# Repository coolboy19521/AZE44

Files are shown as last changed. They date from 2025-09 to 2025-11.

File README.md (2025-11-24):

<h1>AZE - 44 Team Report</h1>



<table align="center" cellspacing="0" cellpadding="0" style="margin:0; padding:0; border-collapse:collapse;">
  <tr>
    <th colspan="2">Team Photos</th>
  </tr>
  <tr>
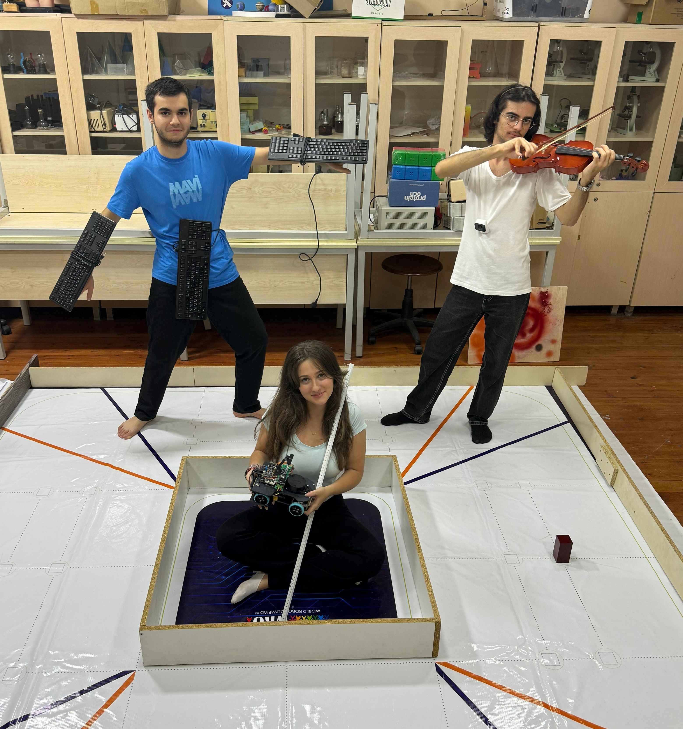
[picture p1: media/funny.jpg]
    <td align="center" style="margin:0; padding:0;"><br><b>Funny Photo</b></td>
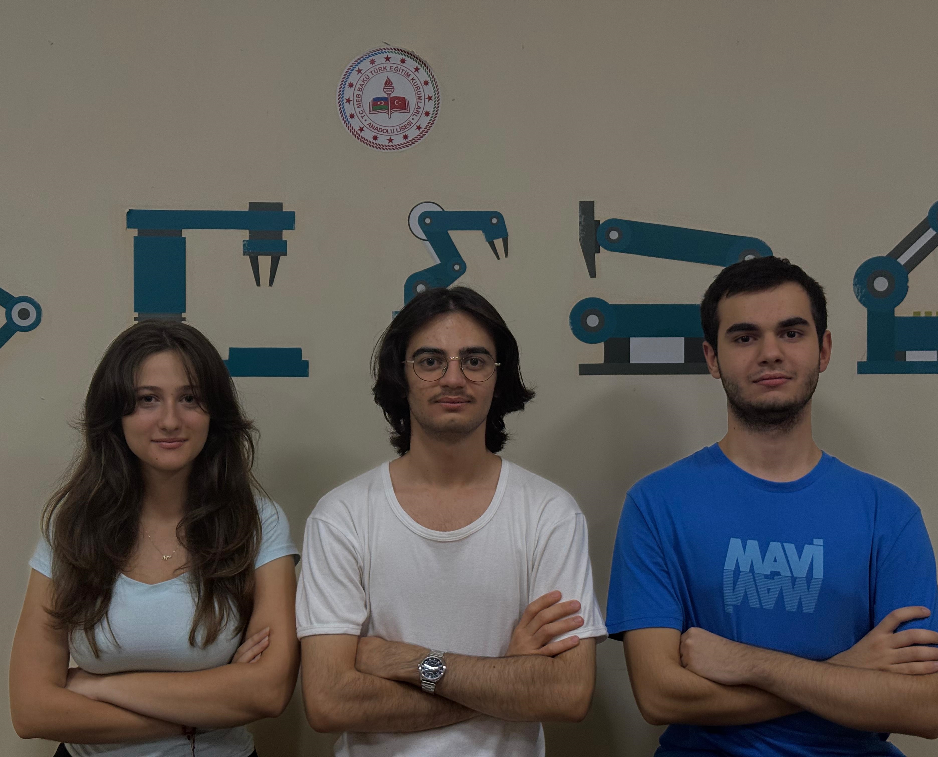
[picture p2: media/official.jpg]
    <td align="center"><br><b>Official Photo</b></td>
  </tr>
</table>

Our team consists of 3 members: Eyyub Şenal (center in the official photo), Əhməd Qəmbərli (rightmost in the official photo), and Melisa Yıldız (leftmost in the official photo). Everyone in this team has an experience of WRO at least at national level. Eyyub and Melisa have even participated at international stages. Eyyub received a silver medal in WRO 2023 Panama and Melisa received a gold medal in WRO 2024 İzmir. Here are communication informations for our team:

- Eyyub Şenal from [Bakı Türk Anadolu Liseyi](https://btal.meb.k12.tr/):
  - <a href="mailto:arduinoaz2022@gmail.com" style="text-decoration:none;">
      
      arduinoaz2022@gmail.com
    </a>
  - <a href="https://www.instagram.com/shenaleyup?igsh=MWpqMHJieTc5MXM1Ng==">
      
      shenaleyup
    </a>

- Əhməd Qəmbərli from [Bakı Türk Anadolu Liseyi](https://btal.meb.k12.tr/):
  - <a href="mailto:ehmedqemberli09@gmail.com">
      
      ehmedqemberli09@gmail.com
    </a>
  - <a href="https://discord.gg/your_discord_invite">
      
      coolboy19521
    </a>

- Melisa Yıldız from [Bakı Türk Anadolu Liseyi](https://btal.meb.k12.tr/):
  - <a href="mailto:melisa.17.yildiz@gmail.com">
      
      melisa.17.yildiz
    </a>
  - <a href="https://www.instagram.com/melisa_yildiz_17?igsh=MWN1cGxsMXF5YndtOQ==">
      
      melisa_yildiz_17
    </a>

> [!NOTE]
> Fun fact: Every pair of our team members' have worked as a team before. It is first time that we are working as a trio.

Before the national qualification our work schedule was very full, we were working every day before the competition. We started in summer so we had plenty of time during the holiday. After qualifying to the international finals we had to limit how much we work every week, because we had school, exams and a **personal life**. We worked every Monday, Wednesday, Thursday and Saturday. On Sundays we had a meeting about the improvements over the week and what we are planning to do next week.

<h1>Our Robot</h1>

<table cellspacing="0" cellpadding="0" style="margin:0; padding:0; border-collapse:collapse;">
  <tr>
    <th colspan="4">Robot Photos</th>
  </tr>
  <tr>
    <td align="center" colspan="2">
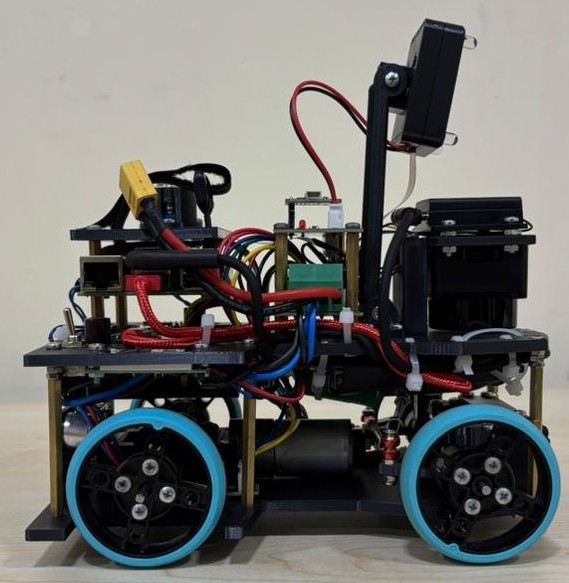
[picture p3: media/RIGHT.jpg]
      <br>
      <b>Right</b>
    </td>
    <td align="center" colspan="2">
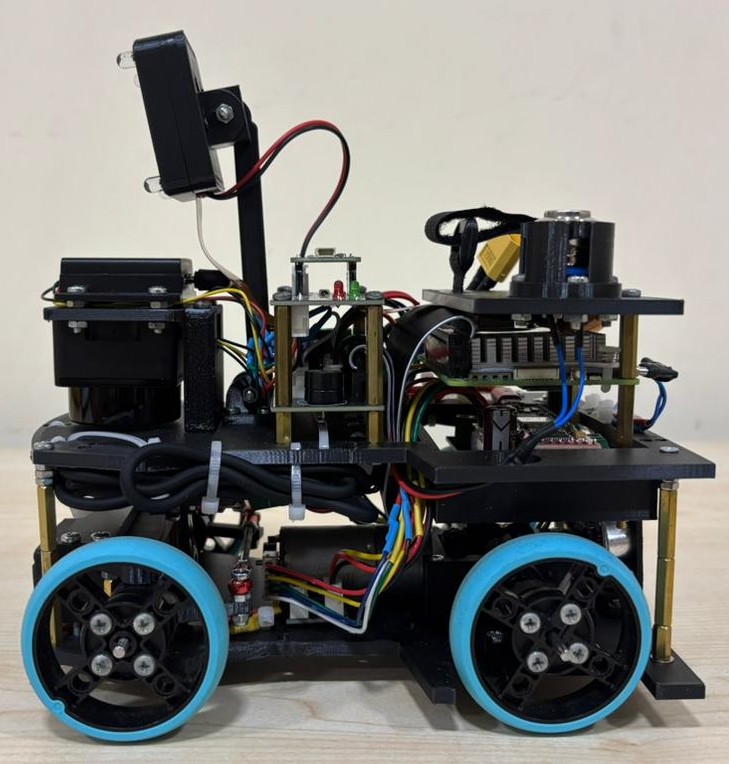
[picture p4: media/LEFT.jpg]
      <br>
      <b>Left</b>
    </td>
  </tr>
  <tr>
    <td align="center">
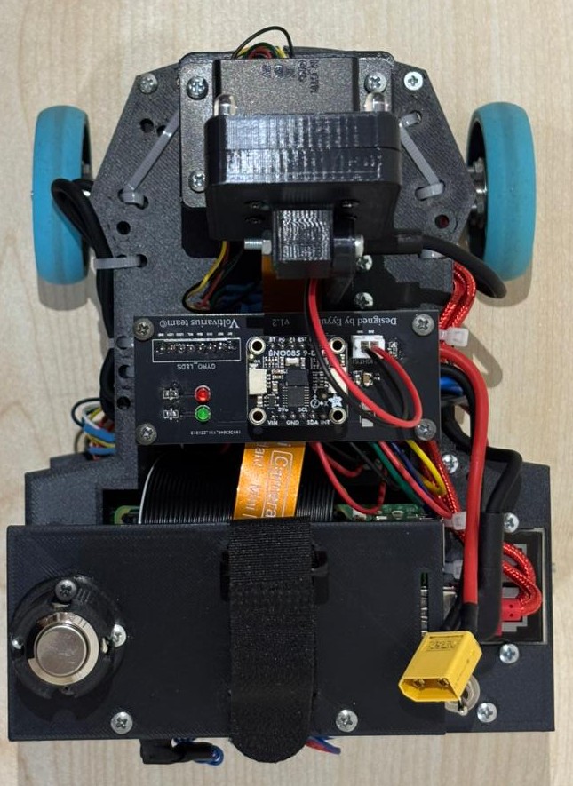
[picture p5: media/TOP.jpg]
      <br>
      <b>Top</b>
    </td>
    <td align="center">
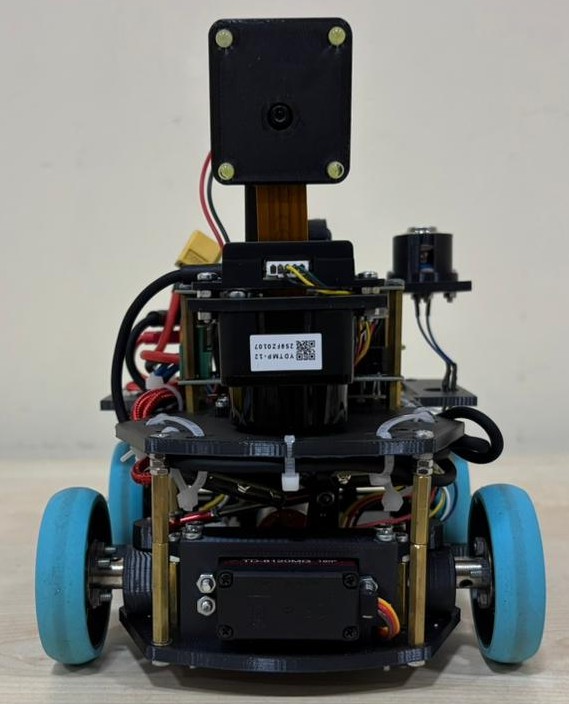
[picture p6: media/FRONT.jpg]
      <br>
      <b>Front</b>
    </td>
    <td align="center">
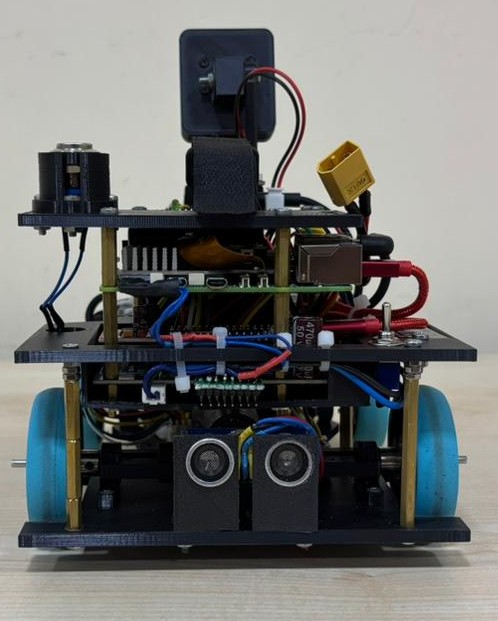
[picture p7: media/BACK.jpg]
      <br>
      <b>Back</b>
    </td>
    <td align="center">
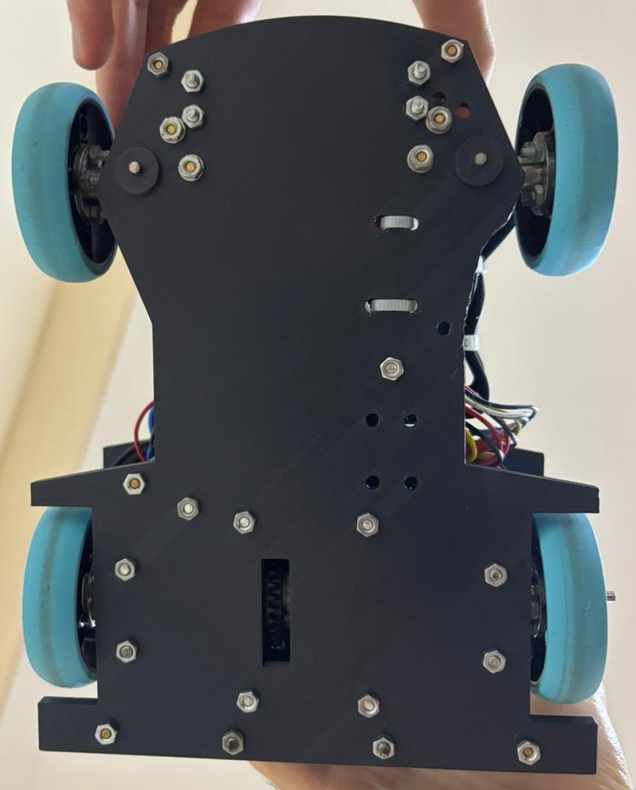
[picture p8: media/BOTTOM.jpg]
      <br>
      <b>Bottom</b>
    </td>
  </tr>
</table>

Our robot is called “miav”. Miav is a ROS2-based four-wheeled mobile robot developed on the Raspberry Pi 5 platform. It integrates advanced hardware including a T-MINI-Plus Lidar TOF, a BNO085 IMU, and a Raspberry Pi Camera for color detection.

<h1>Table of Contents</h1>

### [Evolution of our robot](/EVOL.md)
### [Philosophy and habits](/PHIL.md)
### [Electronics documentation](/schemes/README.md)
### [Mechanics documentation](/models/README.md)
### [Software documentation](/src/README.md)
### [Videos](/videos/README.md)
### [Team photos](/t-photos/README.MD)
### [Robot photos](/v-photos/README.md)
<hr>

<p align="center">
  <picture>
  <source media="(prefers-color-scheme: dark)" srcset="media/my_image.png">
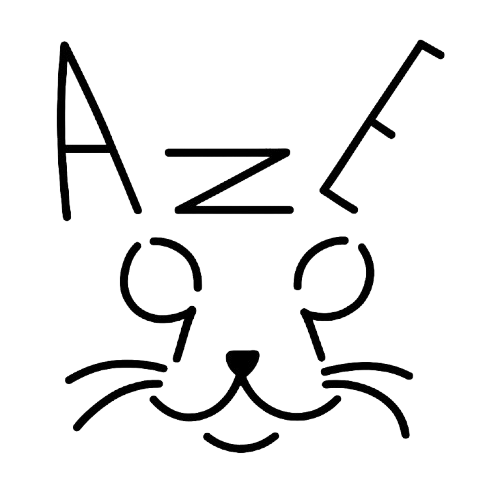
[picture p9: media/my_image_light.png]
  
  </picture>
</p>

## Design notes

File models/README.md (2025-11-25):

>[!IMPORTANT]
>This README file includes some gifs, which could be best viewed through the GitHub itself. You might need to wait for some GIFs to load as well.

>[!IMPORTANT]
>There are some heavy videos inside this README file. Please wait until the page is fully loaded before proceeding.

# 1. Bill of Materials (BOM)

<table align="center">
  <tr>
    <th colspan="4">Mechanics</th>
  </tr>

  <tr>
    <th>Component</th><th>Picture</th>
    <th>Component</th><th>Picture</th>
  </tr>

  <tr>
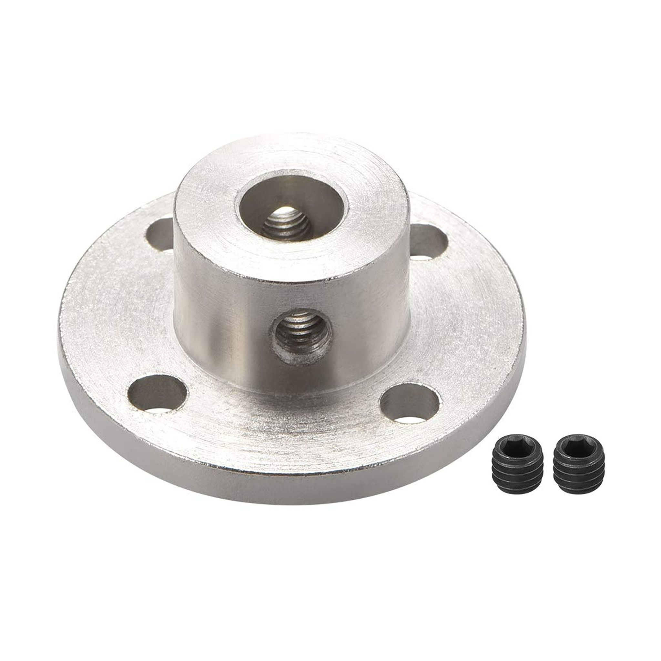
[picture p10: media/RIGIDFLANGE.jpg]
    <td>3mm Rigid Flange Coupling x 4</td><td></td>
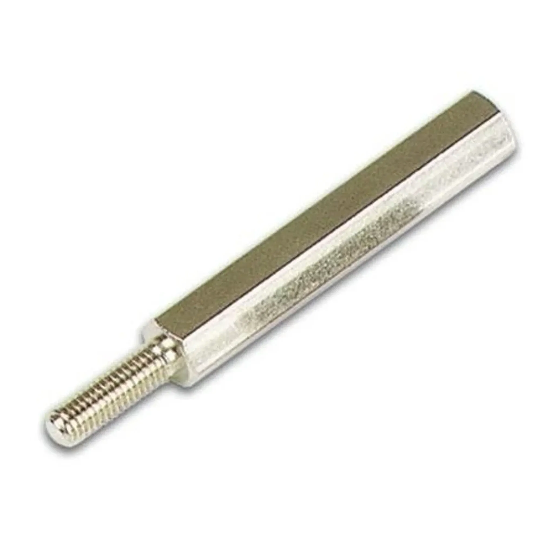
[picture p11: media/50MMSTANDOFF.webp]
    <td>50mm Standoff Female-Male x 6</td><td></td>
  </tr>

  <tr>
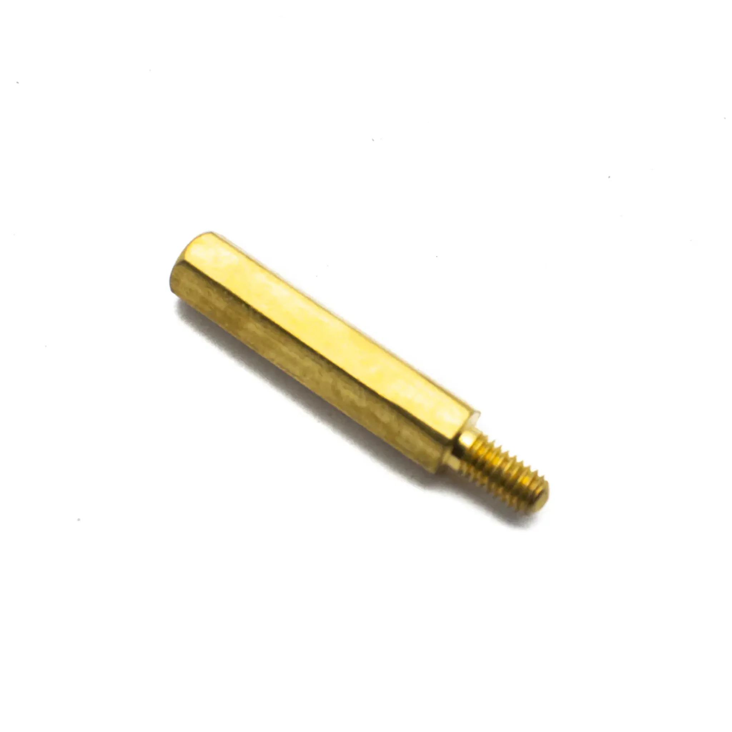
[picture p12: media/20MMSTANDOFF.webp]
    <td>20mm Standoff Female-Male x 4</td><td></td>
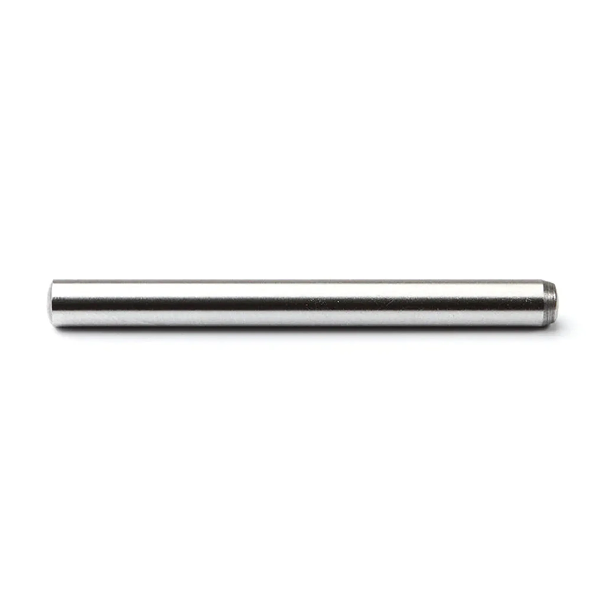
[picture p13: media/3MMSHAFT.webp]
    <td>3mm Shaft 7cm x 2</td><td></td>
  </tr>

  <tr>
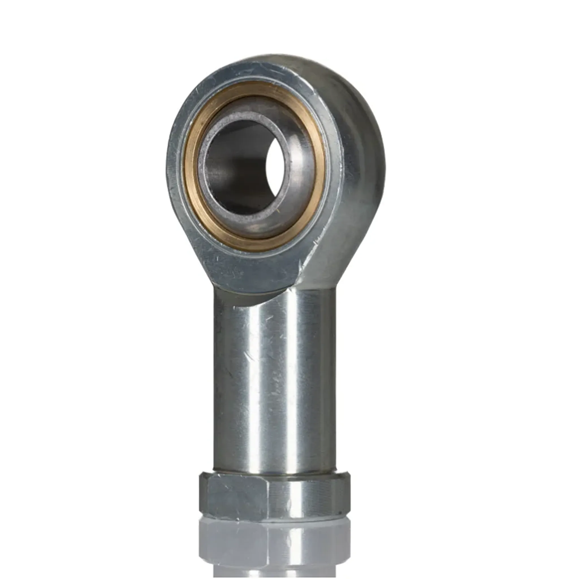
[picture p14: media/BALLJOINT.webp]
    <td>Ball Joint x 4</td><td></td>
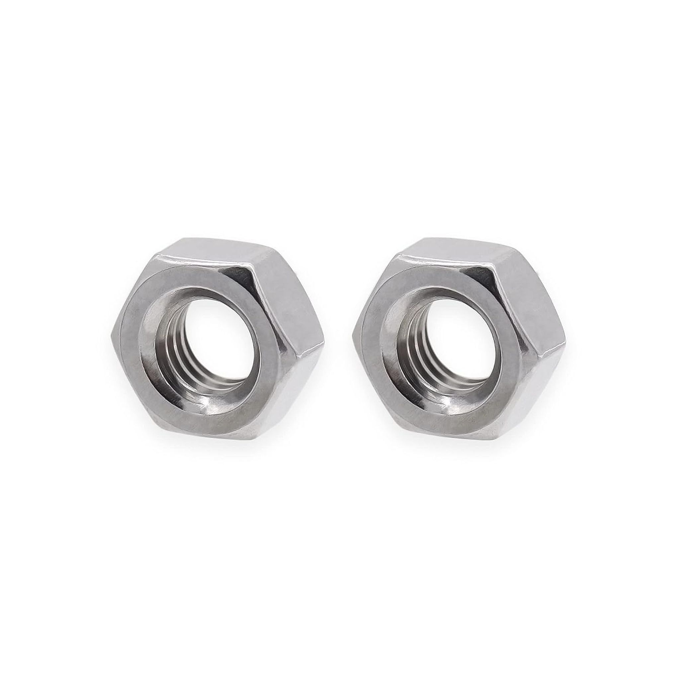
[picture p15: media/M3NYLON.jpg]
    <td>M3 Nylon Insert Lock Nut x 2</td><td></td>
  </tr>

  <tr>
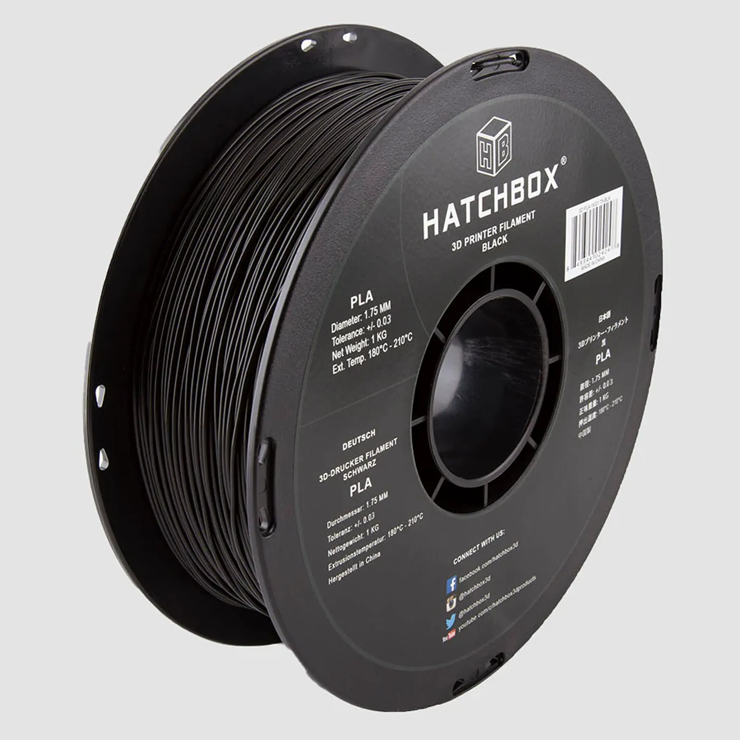
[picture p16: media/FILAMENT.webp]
    <td>Filament 1Kg x 1</td><td></td>
  </tr>
</table>

# 2. The  Chassis and General Design

We have a 2-platform design in our robot, which we preferred to be able to modify or repair the robot easily during our test and potentially the competition.

- It only takes our robot a few seconds to remove its top platform,
- We can access the circuitry, sensors, and other internal mechanics so that we can work on them immediately. This saved us so much time when we working on our robot.

The initial design for our chassis was very narrow with angled corners. Although it was sufficient enough for our initial testing, it was very unstable at higher speeds and tended to tip over easily when we added more parts to it. We first analyzed how our mass is distributed and where our center of gravity is, then we decided to completely revamp our design and resize our chassis to `15cm` in width and `28cm` in length. After the modifications, we were able to increase the stability of our robot so that our sensors, which include the camera and LIDAR, are protected from damage caused by vibrations.

-	We printed the 3D parts with PLA and the Sidewinder X2, 
-	along with a nozzle temperature of `210°C` and a heated bed temperature of `60°C`. Where we felt we needed additional strength, for example, in our shafts and our link rods, we chose to work with aluminum. Additionally, the robot weighs `1400g`.

The earlier versions of robots did not support complex steering or mounting points for sensors and other factors, but with the new design, it has become more modular, and ready for the Ackermann steering mechanism.

<table align="center">
  <tr>
    <th colspan="2">Top Chassis Mechanical Drawings</th>
  </tr>
  <tr>
    <td align="center">
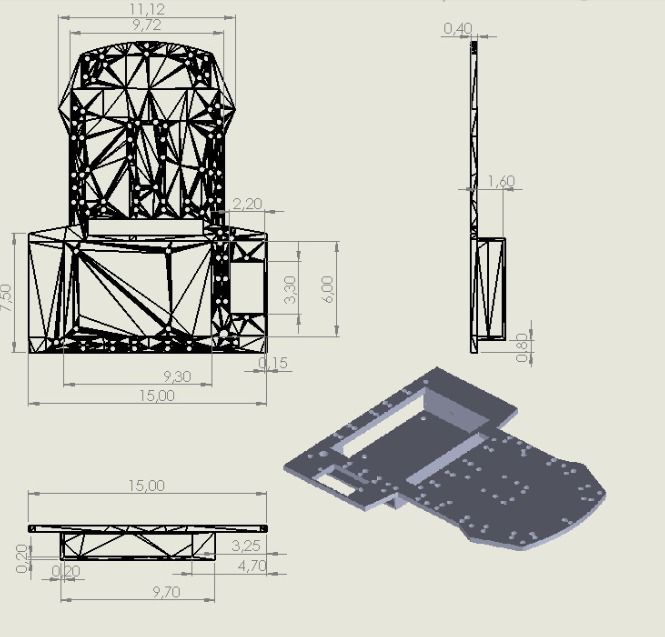
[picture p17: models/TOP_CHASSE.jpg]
      <br>
      <b>Top Chassis</b>
    </td>
    <td align="center">
      <br>
      <b>Printing Proccess</b>
    </td>
  </tr>
</table>
<br>
<table align="center" cellspacing="0" cellpadding="0" style="margin:0; padding:0; border-collapse:collapse;">
  <tr>
    <th colspan="4">Bottom Chassis Mechanical Drawings</th>
  </tr>
  <tr>
    <td align="center" colspan="2">
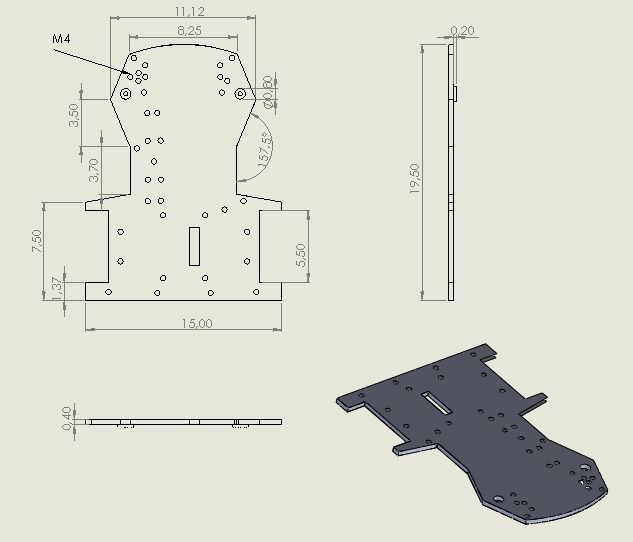
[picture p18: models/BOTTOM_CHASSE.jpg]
      <br>
      <b>Bottom Chassis</b>
    </td>
    <td align="center" colspan="2">
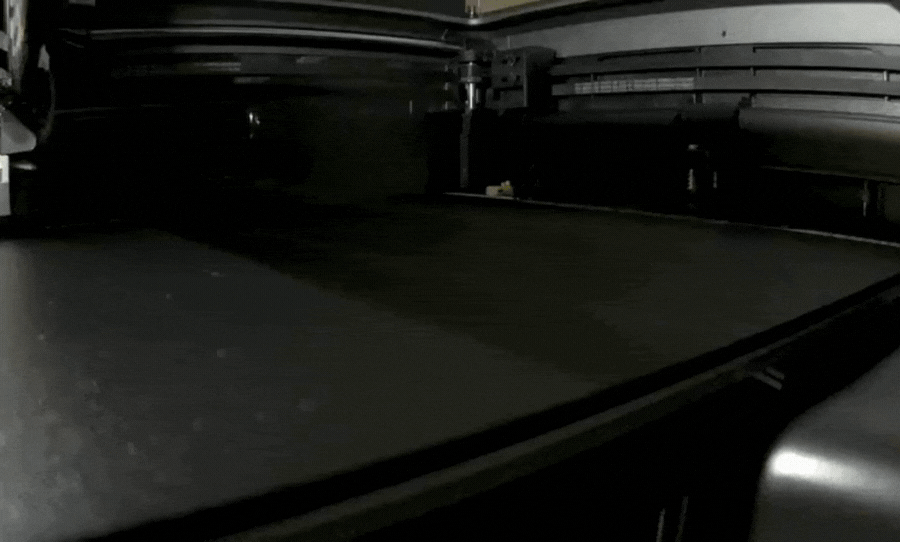
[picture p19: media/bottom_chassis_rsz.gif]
      <br>
      <b>Bottom Chassis Printing Proccess</b>
    </td>
  </tr>
</table>

# 3. Drive System and Gearbox

We use a `12V` DC motor as our drive motor for our robot.

-	It draws about `320mA` on average with no load and revolves at a speed of up to `450RPM`.
-	Although our robot weighs `1400g`, if we rely on this motor directly, it may result in insufficient torque for our robot to glide smoothly, especially when our robot accelerates. Because of this, we decided to create a gearbox to possess a ratio of `2:3` using our 3D printer.

Below is the formula for the torque gained from this ratio:

$$\large T_{\text{output}} = T_{\text{motor}} \times \frac{3}{2}$$

How it works:
- The power generated from the motor is transmitted to the central gear and
- then it is transmitted to the other two wheels in the rear part of the vehicle. 

We also modeled the gearbox to work similarly to how a differential works. This means that when one wheel stops revolving, for example, when it hits something or meets more friction, the other can continue revolving. This way we make sure that it does not get stuck or lose its pace.

We printed the gears themselves and the gearbox with the PLA material, with aluminum shafts on which the gears are mounted. We also placed metal ball bearings on every rotating shaft, including rear wheels and gearbox connections, for our robot to work smoothly, instead of causing excessive wear to our gears to decrease friction. The metal ball bearings are 693ZZ.

<table align="center" cellspacing="0" cellpadding="0" style="margin:0; padding:0; border-collapse:collapse;">
  <tr>
    <th colspan="4">Gearbox Mechanical Drawings</th>
  </tr>
  <tr>
    <td align="center" colspan="2">
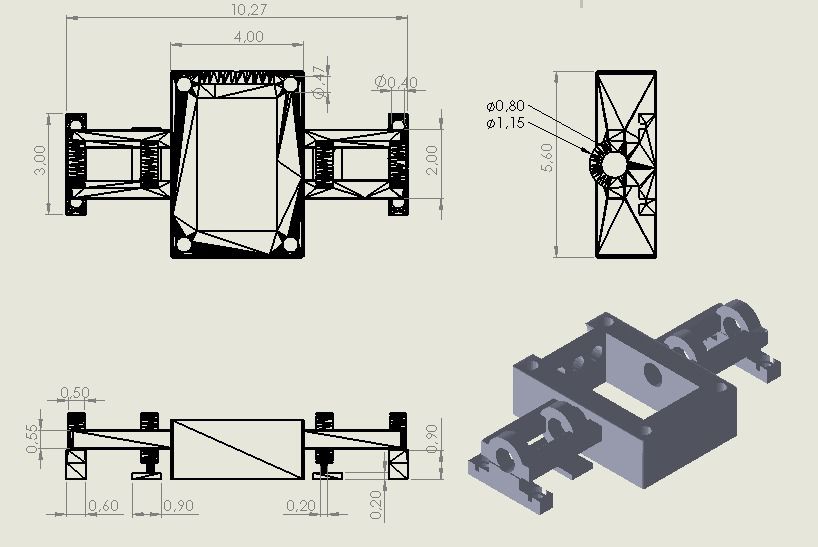
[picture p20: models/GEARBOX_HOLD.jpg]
      <br>
      <b>Gearbox</b>
    </td>
    <td align="center" colspan="2">
      <br>
      <b>Printing Proccess</b>
    </td>
  </tr>
</table>

<br>

<div>
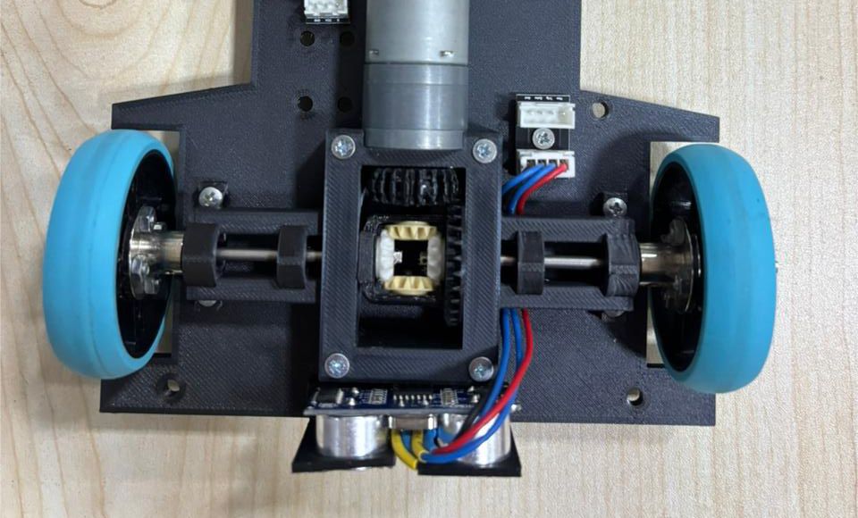
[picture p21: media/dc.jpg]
DC System
  
  <p style="margin-top:0;"><i>Figure 1.1: DC System</i></p>
</div>

# 4. Ackermann Steering System

One of the most important changes that we integrated into our design is the Ackermann steering system. We didn’t use this mechanism in our previous versions of the robots, where we could only manage to implement either turning mechanisms with semi-fixed angles and less accurate steering mechanisms. After we saw the difficulties that the previous systems were causing, wedecided to design the entire steering mechanism from scratch.
The principle behind Ackermann steering is that for a turn, the inner wheel has to turn at a sharper angle than the outer wheel. This corresponds to the geometric shape described by circular motion, where each wheel essentially has to turn at a slightly different radius than the other. After we applied the Ackermann principle, we were finally able to ensure that no wheels start to slide and that the robot moves in predictable arcs.

The formula for the relationship between steering angle is:

$$\large \frac{\tan(\theta_\text{inner})}{\tan(\theta_\text{outer})} = \frac{L}{L + T}$$

L is wheelbase and T is track width. The correct formula using turning radius is:

$$\large \frac{1}{\tan(\theta_\text{inner})} = \frac{1}{R} - \frac{D}{2H} \quad \large ; \quad \large \frac{1}{\tan(\theta_\text{outer})} = \frac{1}{R} + \frac{D}{2H}$$

Our front wheel distance is 13 cm, and our wheelbase (distance between our front and rear axle) is 11 cm. As I’ve already mentioned, the measurements were all established according to the Ackermann mechanism, which ensure that both wheels turn at angles and are still in sync.

In our steering system we used:
-	Aluminum link arms that are mounted to 3D-printed steering knuckles and a PLA servo mount. 
-	We coupled the link arms with 3-mm aluminum rods, and all pivot points are equipped with 693ZZ bearings to ensure uniform movement. 
-	The steering power comes from a TD8120MG metal-gear servo. The servo acts on one link arm, and its action is transmitted through the Ackermann design to turn the wheels by the right amount. This way we make sure that our robot has a smooth turning action.

It is also important to notice and emphazie that the Ackermann steering is implemented in actual vehicles as well,
-	To reduce wear on tires, 
-	Enhance turning precision, and 
-	Provide better control at both high and low velocities. For us, its implementation in our robot allowed our vehicle to act similarly to actual vehicles and enhance the turning precision in our navigation significantly.

<table align="center">
  <tr>
    <th colspan="2">Ackermann Wheel Holder Mechanical Design</th>
  </tr>
  <tr>
    <td align="center">
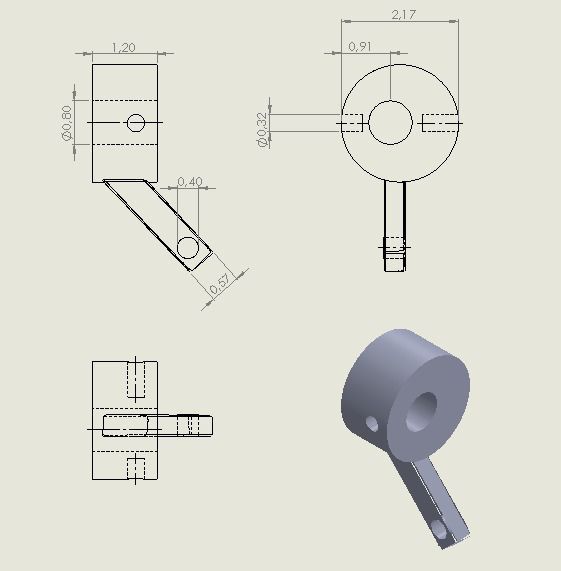
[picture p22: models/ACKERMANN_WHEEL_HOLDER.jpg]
      <br>
      <b>Ackermann Wheel Holder</b>
    </td>
    <td align="center">
      <br>
      <b>Printing Proccess</b>
    </td>
  </tr>
</table>

<br>

<div>
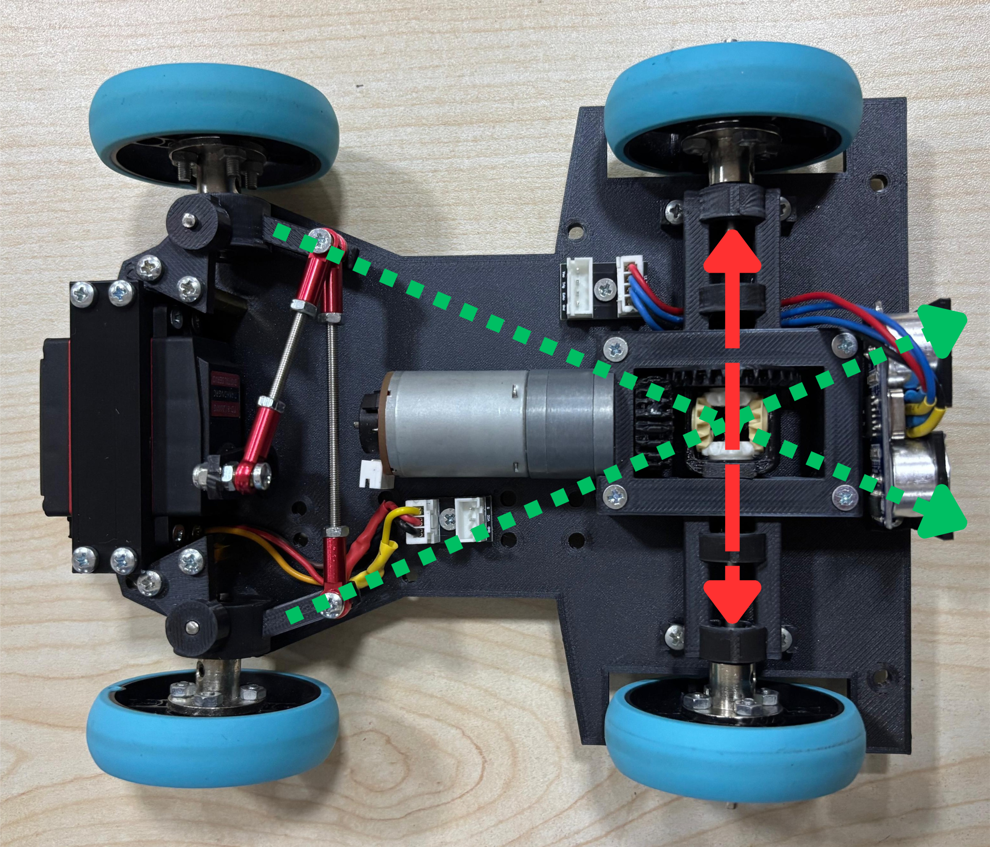
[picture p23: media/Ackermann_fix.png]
Ackermann System
  
  <p style="margin-top:0;"><i>Figure 2.1: Ackermann System</i></p>
</div>

>[!NOTE]
>The dotted lines here represent the imaginary projection of a straight line aligned perfectly with the tire holders. The intersection point of these lines should align to the center of the track perfectly for a functional ackermann system. In our previous robot we had miscalculated it a little bit, and the intersection point was a little bit away from the track. That's why this time we focused on fixing the problem. An accurate ackermann system provides us better steering possibilities.

# 5. Servo System

The servo that controls the steering mechanism is the TD8120MG metal gear servo. It has a torque of around 18 kg-cm at 4.8 volts and about 20 kg-cm at 6 volts, which is ideal for the rotation of the wheels. The servo also requires about 1.1 seconds to rotate 360 degrees, so it enables fast steering.

We placed the servo on top of a bracket created using PLA, and we specifically designed this bracket to make sure that it aligns well with the Ackermann linkage mechanism. As the servo rotates, it acts on the main steering arm, which in turn acts on both front wheels using the Ackermann rods.

<table align="center" cellspacing="0" cellpadding="0" style="margin:0; padding:0; border-collapse:collapse;">
  <tr>
    <th colspan="4">Servo Holder Mechanical Design</th>
  </tr>
  <tr>
    <td align="center" colspan="2">
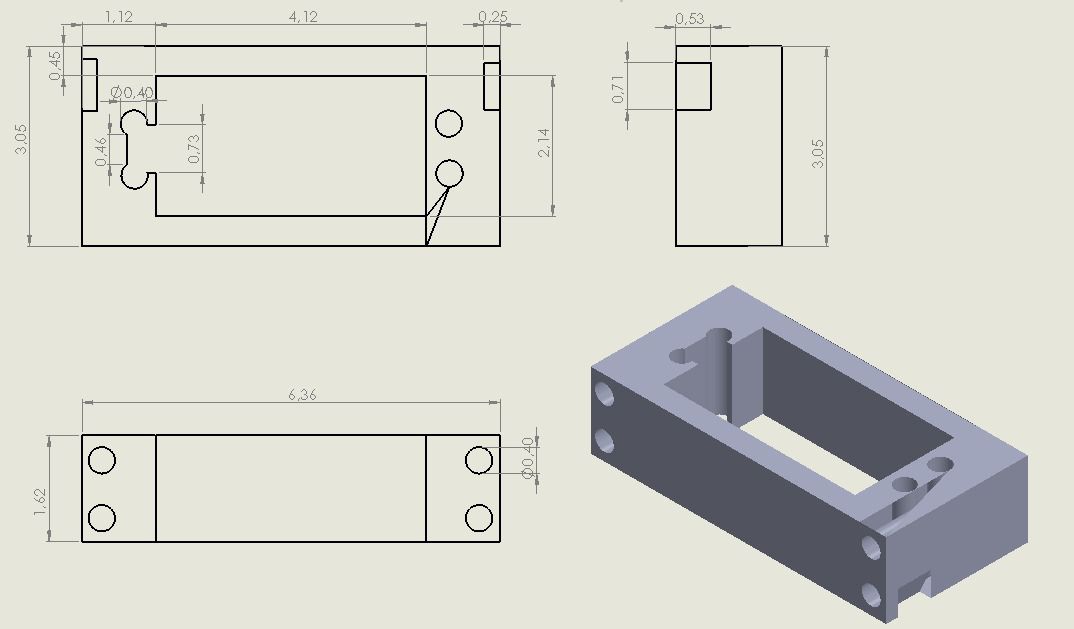
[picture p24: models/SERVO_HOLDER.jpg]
      <br>
      <b>Servo Holder</b>
    </td>
    <td align="center" colspan="2">
      <br>
      <b>Printing Proccess</b>
    </td>
  </tr>
</table>

# 6. Wheel Movement
-	We control the movement of the wheels on our robot with the rear DC motor. As the rear wheels rotate clockwise, they propel the robot forward.
-	The the rotation of the motor in an anticlockwise direction makes the robot go backward. 
-	With the gearbox on the robot we are able to ensure that if one wheel faces a rotation problem or a mechanical barrier in general, the other wheel continues to rotate.

# 7. Center of Gravity and Weight Distribution
We also positioned every element on our robot to ensure its center of mass remains near the center. Liked this, we increase the robot’s balance and make sure it doesn't develop nose or tail lift during acceleration or braking.

-	We placed The LIDAR near to the front but slightly above the center because we wanted to provide our robot with a full scan range. 
-	The camera sensor is placed on its 75-degree width-wise PLA bracket to allow it to scan most of its environment and identify objects-the colors-effectively. 
-	Lastly, at the back, we mounted the ultrasonic sensor to assist our robot in detecting objects while reversing or turning through its track on the map.
-	In the middle of the bottom platform, we put the battery that helps balance out the heavier parts on top, such as the Raspberry Pi and motor driver. We placed the components in this particular way because we wanted our vehicle to have very stable movement when driving, especially during higher speeds while turning.

The formula of the center of mass is:

$$\large X_\text{cm} = \frac{\sum_{i=1}^{n} x_i \times m_i}{\sum_{i=1}^{n} m_i} \quad \large ; \quad Y_\text{cm} = \frac{\sum_{i=1}^{n} y_i \times m_i}{\sum_{i=1}^{n} m_i} \quad \large ; \quad Z_\text{cm} = \frac{\sum_{i=1}^{n} z_i \times m_i}{\sum_{i=1}^{n} m_i}$$

So applying this formula to our robot:

- Total mass $$\large \text{M}$$ = 1400 g.
- Coordinate system: (0,0) = front-left corner. 𝑥to the right (0–15 cm), 𝑦to the rear (0–19 cm).
- Component positions $$\text{(x, y)}$$ in cm and masses 𝑚in g:
1.	Battery: $$\large \text{m}$$ = 300, $$\text{(x, y)}$$ = (4,1)
2.	Raspberry Pi: $$\large \text{m}$$ = 45, $$\text{(x, y)}$$ = (4,1)
3.	Lidar: $$\large \text{m}$$ = 18, $$\text{(x, y)}$$ = (7.5,2)
4.	Servo: $$\large \text{m}$$ = 55, $$\text{(x, y)}$$ = (7.5,6)
5.	Encoder motor: $$\large \text{m}$$ = 120,	$$\text{(x, y)}$$ = (2,16)
6.	Motor driver: $$\large \text{m}$$ = 40, $$\text{(x, y)}$$ = (7.5,9)
7.	Camera: $$\large \text{m}$$ = 10,	$$\text{(x, y)}$$ = (7.5,0.5)
8.	BNO085: $$\large \text{m}$$ = 8,	$$\text{(x, y)}$$ = (6,10)
9.	Ultrasonic : $$\large \text{m}$$ = 15,	$$\text{(x, y)}$$ = (7.5,19)
10.	Amper monitor: $$\large \text{m}$$ = 30,	$$\text{(x, y)}$$ = (10,12)
11.	Misc (connectors, resistors, fuse, SD, etc.): $$\large \text{m}$$ = 20, $$\text{(x, y)}$$ = (7.5,9)
12. Chassis + mechanical + wheels: $$\large \text{m}$$ = 739, $$\text{(x, y)}$$ = (7.5,9.5)

$$\large \sum_{i=1}m_i$$ = 300 + 45 + 18 + 55 + 120 + 40 + 10 + 8 + 15 + 30 + 20 + 739 = 1400 g

$$\large \sum_{i=1}m_i \times x_i$$ = 1200 + 180 + 135 + 412.5 + 240 + 300 + 75 + 48 + 112.5 + 300 + 150 + 5542.5 = 8695.5

$$\large X_\text{cm} = \frac{\text{8695.5}}{\text{1400}} = \text{6.21 cm}$$

$$\large \sum_{i=1}m_i \times y_i$$ = 300 + 45 + 36 + 330 + 1920 + 360 + 5 + 80 + 285 + 360 + 180 + 7020.5 = 10921.5

$$\large Y_\text{cm} = \frac{\text{10921.5}}{\text{1400}} = \text{7.8 cm}$$

This helped us create a well-rounded robot that moves in a predictable manner and doesn't tip.

<table align="center" cellspacing="0" cellpadding="0" style="margin:0; padding:0; border-collapse:collapse;">
  <tr>
    <th colspan="1">Mass Diagrams</th>
  </tr>
  <tr>
    <td align="center" colspan="2">
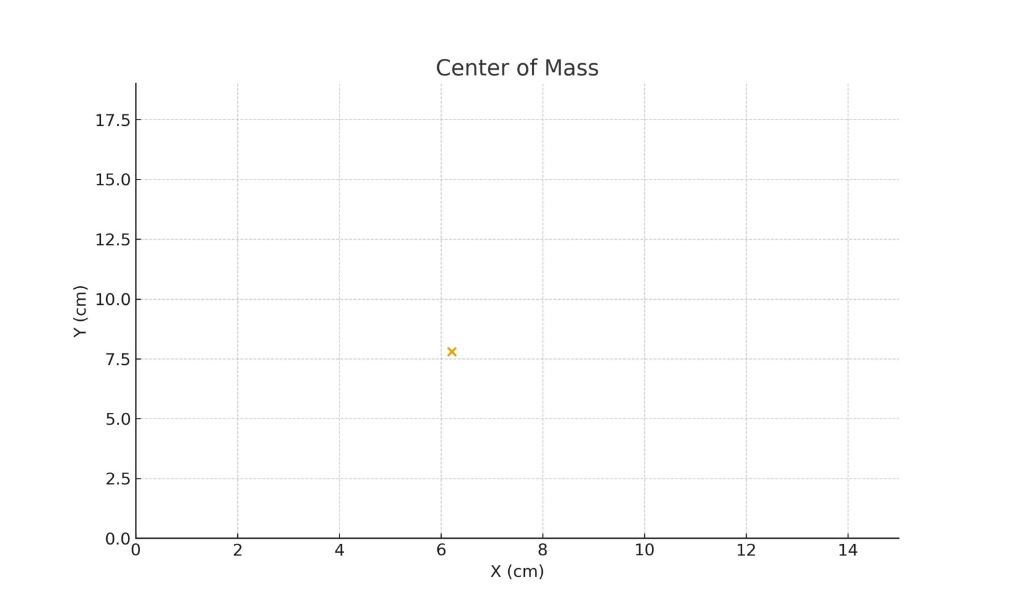
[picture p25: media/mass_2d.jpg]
      <br>
      <b>Mass Diagram 2D</b>
    </td>
  </tr>
</table>

# 8. Cable Management

We organized every cable on our robot,  using PLA holders. We used them solely for this function, ensuring that we segregate the power cables, data cables, and servo cables so they are free from any interaction with electromagnetic interference, which can potentially lead to erratic behaviors or data from our sensor or servo. You can also see in our design that our cables are secured to prevent them from shifting whenever our robot moves.

# 9. Mechanical Materials and Bearings

-	We preferred to work with PLA for 3D parts because it is light and has easy printing properties. 
-	In parts that needed higher strength such as shafts, rods, or arms in linkages, we chose to work with aluminum because it resists deformation under stress but still is light.
-	For all turning joints, we used 693ZZ metal ball bearings. Metal ball bearings serve to reduce friction and vibration within the drivetrain, turning pivots, and wheel axles.
-	We mounted bearings on the gearbox and front steering pivots to provide smooth motion and enhance mechanical robustness.

<table align="center" cellspacing="0" cellpadding="0" style="margin:0; padding:0; border-collapse:collapse;">
  <tr>
    <th colspan="4">Robot Solidworks Photos</th>
  </tr>
  <tr>
    <td align="center" colspan="2">
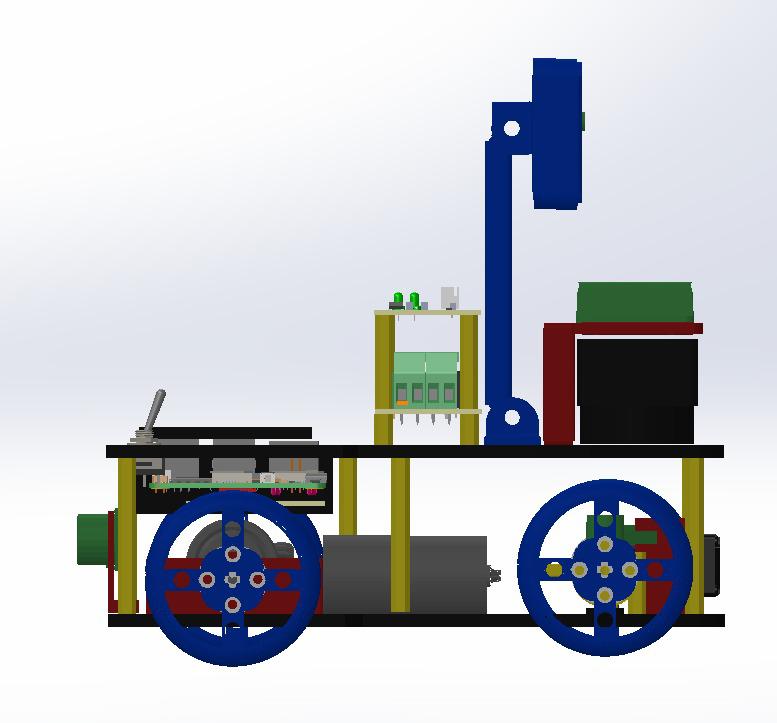
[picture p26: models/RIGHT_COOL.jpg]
      <br>
      <b>Right</b>
    </td>
    <td align="center" colspan="2">
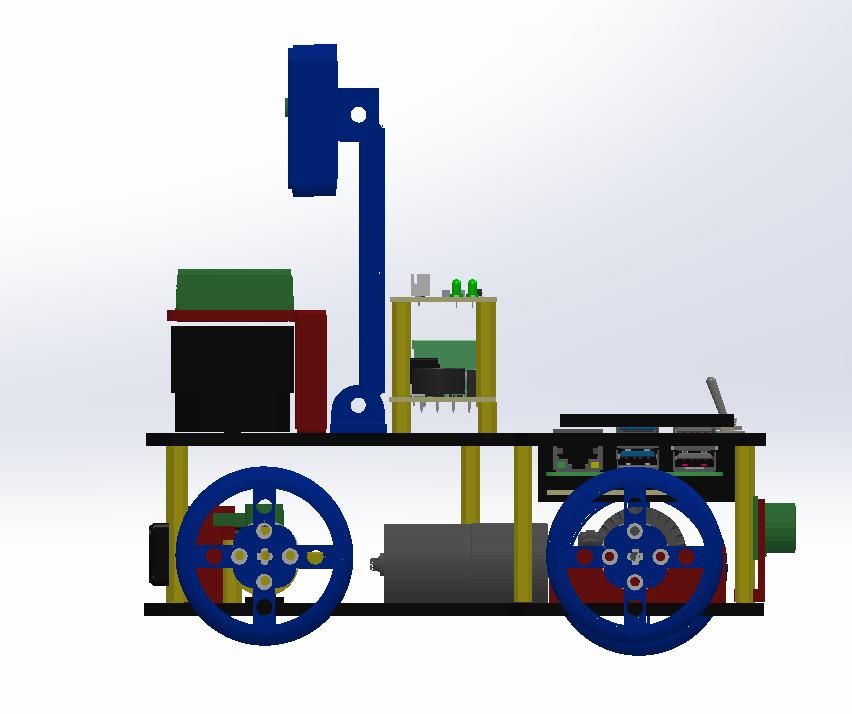
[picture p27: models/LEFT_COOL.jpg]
      <br>
      <b>Left</b>
    </td>
  </tr>
  <tr>
    <td align="center">
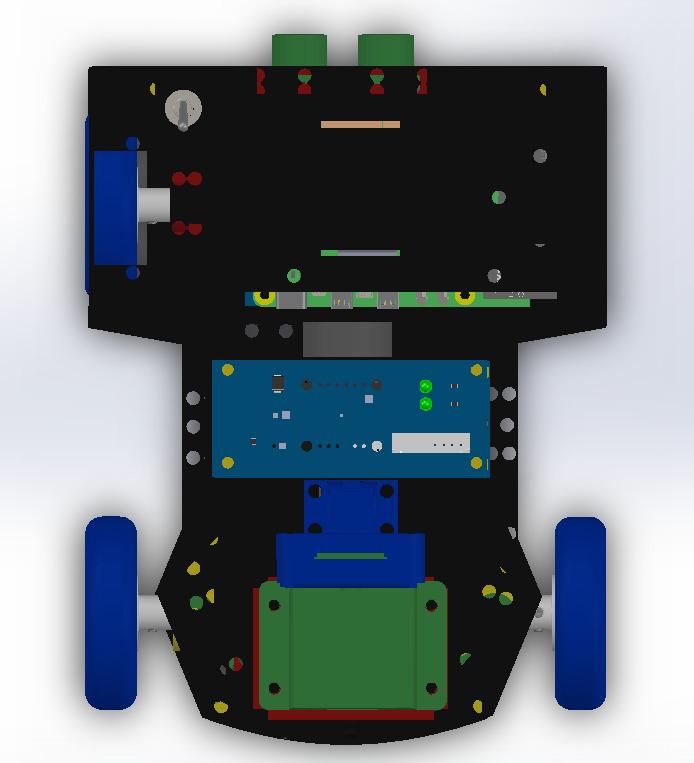
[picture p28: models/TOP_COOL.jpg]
      <br>
      <b>Top</b>
    </td>
    <td align="center">
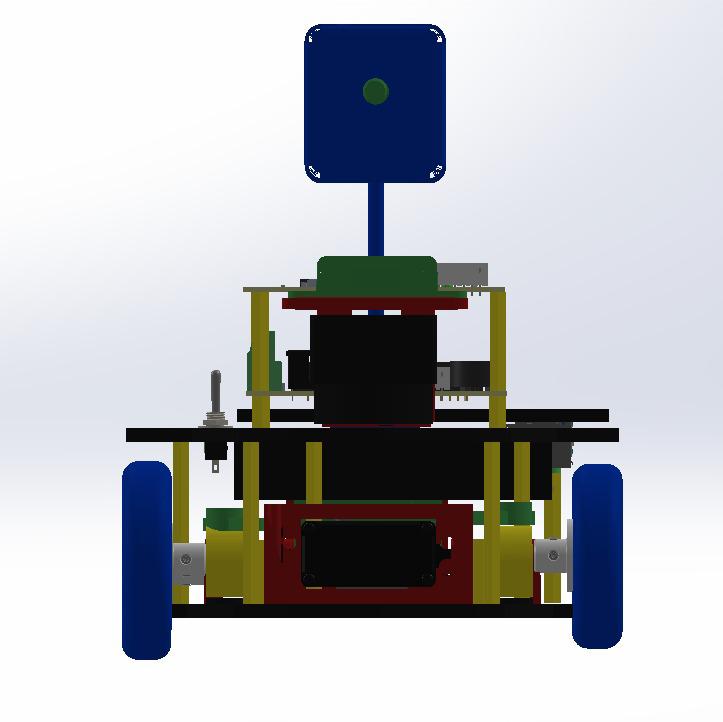
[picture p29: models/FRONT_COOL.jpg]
      <br>
      <b>Front</b>
    </td>
    <td align="center">
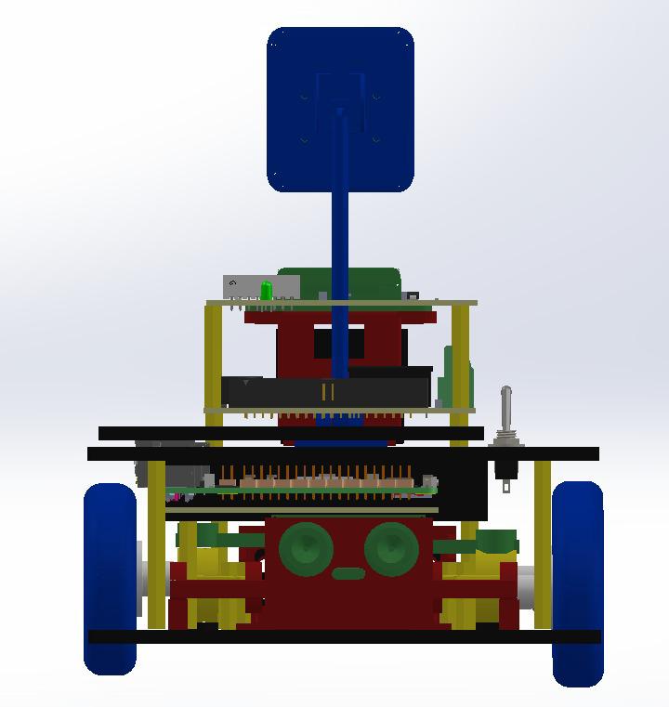
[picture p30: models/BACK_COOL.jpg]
      <br>
      <b>Back</b>
    </td>
    <td align="center">
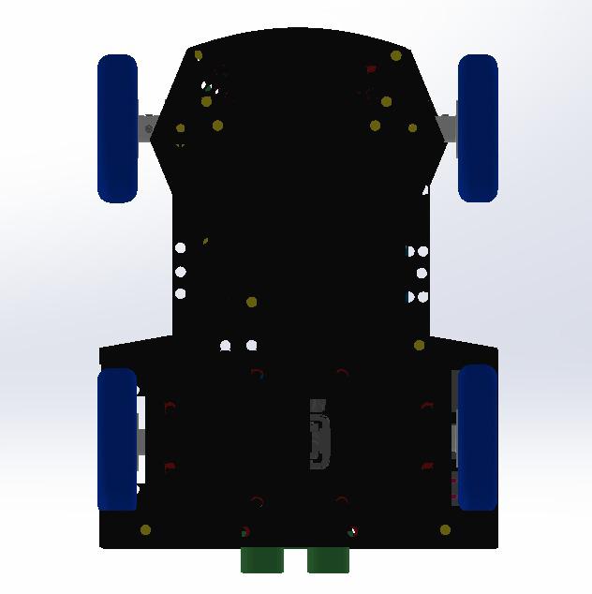
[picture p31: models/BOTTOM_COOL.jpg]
      <br>
      <b>Bottom</b>
    </td>
  </tr>
</table>

# 10. Sensor and Component Placement

-	As mentioned before, we placed the LIDAR is placed at the front for it to scan freely from its environment. 
-	Coming to the front-mounted camera, we positioned it upwards for better visibility. 
-	The ultrasonic sensor in the back gives data on the distance behind it, which is really helpful for us during sharp movements and reversing functions in initial tests. 
-	On top are the Raspberry Pi 5 and motor driver, as connectivity is kind of easier there, on the top platform. 
-	We placed the battery to make sure that the center of the mass remains as we intended it to be. 
-	The servo stays on the left side and is directly joined with the main steering arm so it can effectively steer the Ackerman linkages.

<table align="center" cellspacing="0" cellpadding="0" style="margin:0; padding:0; border-collapse:collapse;">
  <tr>
    <th colspan="4">Sensor Placement</th>
  </tr>
  <tr>
    <td align="center">
      <br>
      <b>Camera, Gyro and Lidar from top view</b>
    </td>
    <td align="center">
      <br>
      <b>The ultrasonic sensor from back view</b>
    </td>
  </tr>
</table>

# 11. Specifications for 3D Printing 

-	We used the 3D printer Sidewinder X2 for both replicas and original parts. 
-	Because we use PLA, prints are a lot more accurate, with very low warpage. 
-	The nozzle temperature is at `210°C` and the hot plate temperature is at `60°C` which provides better bonding. 
-	We created time-lapse videos to basically show how each part is being created so that we would be able to evaluate and, if needed, enhance the mechanical aspects of the robot.

<div>
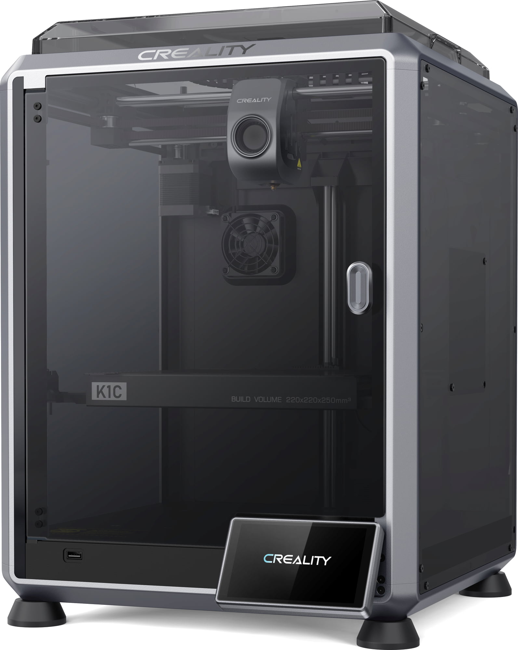
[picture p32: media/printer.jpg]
  
  <p style="margin-top:0;"><i>Figure 3.1: Our printer</i></p>
</div>

# 12. Exploded View and SolidWorks Assembly

We created an exploded view assembly diagram using SolidWorks to detail and better show the development of our robot.

-	We really focused on creating the exploded view to develop the assemblies and the overall robot structure to be certain that the designed mechanism is really going to work in real life. 
-	This way, we made sure that every element of our robotic design was correctly integrated before 3D printing, making us avoid prototype failures. 
- When it comes to the assemblies, you can see the measurement of every mechanical component from every perspective.
-	Keeping the assemblies detailed made it easier for us to go forward with the printing process without any problems. 
-	We also thoroughly discussed which 3D modelling tool to use and concluded that, in comparison to other 3D modeling software, SolidWorks provides better capabilities for working with mechanical assemblies, like interference detection and assembly simulations. 

<div>
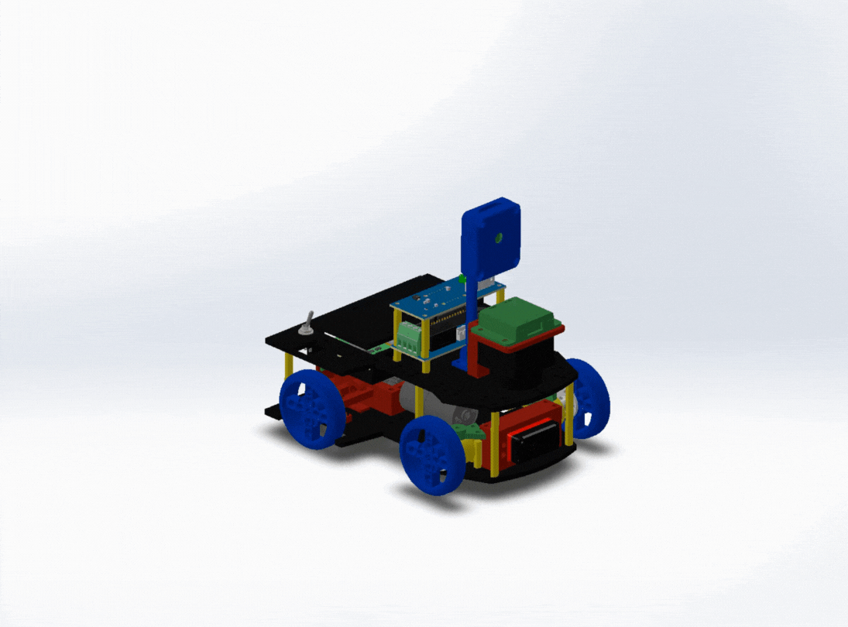
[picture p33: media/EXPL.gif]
  
  <p style="margin-top:0;"><i>Figure 4.1: Exploded View</i></p>
</div>

As you can see, we showed how each part, layers for the chassis, Ackermann steering, gears, sensors, and electronics, combines into a full assembly. 

<hr>

<p align="center">
  <picture>
  <source media="(prefers-color-scheme: dark)" srcset="../media/my_image.png">
  
  </picture>
</p>

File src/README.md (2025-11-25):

>[!IMPORTANT]
>This README file includes some gifs, which could be best viewed through the GitHub itself. You might need to wait for some GIFs to load as well.

>[!IMPORTANT]
>There are some heavy videos inside this README file. Please wait until the page is fully loaded before proceeding.

# 1. Software Structure and Principles 

In this section of the documentation software solution of our strategy is discussed. Before starting to explain how our code works we would like to present our principles while creating the software:

1. **Keep it simple**: The computing power of our SBC and the accuracy of our sensors are limited. There is no point in designing an extra accurate algorithm, because it most probably would not work in practice most of the time. Also maintaining a complex algorithmic structure is not easy and would require a lot of time, which we could more effectively spend on optimizing existing simpler algorithms or our strategy.

2. **Have a margin of error**: There is nothing such as "*at STP*" in the competition arena. So you can't just solely rely on robot's mechanic design and right perfect code. Software should always be able to tolerate some amount of hardware error. So should hardware, as perfection lies in balance of both.

3. **Test enough**: Sometimes we get new ideas for our strategy or overall robot behaviour. It is not appropriate to use it if it works once. Before moving on and accepting the solution, it should be tested. Many of the ideas look bright at first glance but with proper testing its faults are much more observable.
> [!NOTE]
> For every problem, there is a solution which is simple, fast, and wrong.

4. **Never be afraid of trying new ideas**: Most of our ideas about the robot and strategy has changed since we started working on the actual map. Almost nothing has stayed the same. Because of that, we always think of alternative ways of doing something in parallel to implementing our already existing ideas.

5. **Stay positive**: It is really easy to get pessimistic when a solution does not work, especially when you spend a lot of time on it. In times like these we remind ourselves why we started this journey. To learn something new, experience new stuff and compete fairly.

Now that we got our principles out of the way, we can start with the actual software. Our structure for software flow is such:

<div>
  Diagram
  <p style="margin-top:0;"><i>Figure 1.1 Software Flow Diagram</i></p>
</div>

# 2. Implementation details

### 2.1 Motor Driver

From now on we will talk about different sections of the software as described in figure 1.1.

Let's start with the Raspberry Pi Pico - motor driver. We have created our own API for motor and servo control which also supports motor encoders. Before developping our own motor driver we actually tried an already existing one, but it had many issues. The motor driver we used before was consistently losing connection with Raspberry Pi. It was stopping to receive any commands transmitted from the Raspberry Pi and executed the last one. We had many ideas to fix this issue:

1. **Sending large packets over USB**: Our idea for this happening was incorrect use of available transmission space inside the USB adapter. So we modified the API of our previous motor driver. This hypothesis was actually correct to some degree: before making the modification our robot lost connection at approximately `5th minute` of working, but after making the modification we actually quadrupled this number with `20 minutes` lifespan. But robot was still losing connection.

2. **Sending too much motor commands**: This was another hypothesis of ours, and to try it out we lowered the frequency of our Raspberry Pi solution. This actually helped a lot as now the lifespan of the motor driver was up to `40 minutes`. This was some improvement, but motor drivers are designed to work as much as they are powered, not periodically.

3. **Losing bytes when receiving the packets**: We had really good faith in this idea. Because we thought the issue was most probably this. But when we tried adding addition checksums and start flags to the packet for security, nothing changed at all. We did not observe any improvement in lifespan of the motor driver.

After having these issues we decided it was not worth risking a faulty motor driver. When we made this decision there was only a week left before the national qualifications so we were too late to buy a new motor driver. That's why we decided to make our own using Raspberry Pi Pico. Pico receives the commands from Raspberry Pi and sends them to the internat motor driver. When designing the work flow of our API we relied on our previous hypothesis of why a motor drive could fail. The new API we have created has never failed since we have created it and we hope it will stay so. Let's look at some cruicial parts and explain them on code:

```python
while True: # While Pico is alive
    position = encoder.position # Get current position
    if position != last_position: # If current position is not same as last position
        send_command(position) # We send new encoder value
        last_position = position # And update last position

    time.sleep(0.001) # Add a little delay
```

We are only sending when the encoder value changes. Because if we'd always send encoder value usb data storage would be extremely polluted by zeros, and it results in slip.

```python
def read_command():
    global buffer
    if usb_serial.in_waiting > 0:
        buffer += usb_serial.read(usb_serial.in_waiting) # Accumulate buffer globally
    while len(buffer) >= 3: # All packets are siz of 3
        frame = buffer[:3]
        servo_val = frame[0]
        motor_raw = frame[1]
        checksum = frame[2]
        if checksum == ((servo_val + motor_raw) & 0xFF): # If checksums match
            motor_val = motor_raw
            if motor_val >= 128: # Packets are unsigned but to give negative speeds
                motor_val -= 256 # we subtract 256 when speed is over 128.
            buffer = buffer[3:]  # This idea comes from how two's complement works.
            return servo_val, motor_val
        else:
            buffer = buffer[1:] # If checksums mismatch we shift by a byte.
    return None
```

Commands are stored in 2 bytes. The first byte is for steering value and the second one is for motor speed. The byte for motor speed is unsigned, which means it can only take positive values from `0 to 511`. To transform this byte into a signed one, we subtract `256` if the value is greater than `128`. This is how [two's complement](https://en.wikipedia.org/wiki/Two%27s_complement) works. If explained with simple words, the first bit of the byte is for showing if the number is positive or negative and the other bytes add up to the value. As we might need to go back (which requires a negative speed for the motors) we need to support signed bytes. But we don't need a signed byte for steering angle, as it is a value in range `0° - 180°`. Let's take a look at an example command as two bytes:

$${\color{while}Command: \space \color{blue}0010 \space \color{blue}0000 \space \color{lightgreen}0000 \space \color{lightgreen}1101}$$

Here $${\color{blue}0010 \space \color{blue}0000}$$ is the first byte and also the steering value. The binary value of `0010 0000` corresponds to `32`. This means that the steering command our robot has sent is `32°` in range of `0° - 180°`. This translates to `-68°` if we consider the robot's initial steering as `0°`. This value is later sent to the servo in this code snippet:

```python
def set_angle(head): # Head is decoded steering value from the received command.
    head = max(min(head, 180), 0) # Normalize the steering angle.
    us = MIN_US + (MAX_US - MIN_US) * head / 180 # Convert it into PWM values.
    duty = int(us * 65535 / (1_000_000 / SERVO_FREQUENCY)) # Convert it into duty cycle.
    pwm_c.duty_cycle = duty # Set the duty cycle parameter to what we calculated.
```

In electronics, duty cycle's wave length determines the angle of the servo. In this code snippet we calculate the duty cycle according to the steering value we calculated.

Now $${\color{lightgreen}0000 \space \color{lightgreen}1101}$$ is the motor value. This binary value translates to `21` in decimal. As it is less than `128` we do not need to do any proccessing over this value and send this command directly to the motors:

```python
def move_motor(speed):
    if not -100 <= speed <= 100: # If the received speed is not in the allowed range.
        pwm_a.duty_cycle = MAX_PWM # Setting max_pwm do both duty_cycles
        pwm_b.duty_cycle = MAX_PWM # makes the motors hard brake.
    else:
        # Calculate the pwm value in range from MIN_PWM to MAX_PWM.
        pwm_value = int((MAX_PWM - MIN_PWM) * abs(speed) / 100) + MIN_PWM

        if speed > 0: # If it is positive we move forward.
            # To move forward
            pwm_a.duty_cycle = pwm_value # We set gate a to a certain value
            pwm_b.duty_cycle = 0 # and zero out gate b.
        elif speed < 0: # If it is negative we move backward.
            pwm_a.duty_cycle = 0 # We zero out gate a
            pwm_b.duty_cycle = pwm_value # and set gate b to a certain value
        else: # If the value is zero directly
            pwm_a.duty_cycle = 0 # We set both gates to zero.
            pwm_b.duty_cycle = 0 # This makes the robot soft brake.
```

Motors are also controlled via duty cycles. You may have noticed some kind of a gate logic in the code. Most motor drivers have this logic. If you let a flow from gate a and zero out gate b motor moves in a certain direction, and if you do the opposite motor moves in the opposite direction. Refer to the table below for more understanding:

<table align="center" cellspacing="0" cellpadding="0" style="margin:0; padding:0; border-collapse:collapse;">
  <tr>
    <th colspan="4">Motor Driver</th>
  </tr>
  <tr>
    <th>Gate A</th>
    <th>Gate B</th>
    <th>Result</th>
  </tr>
  <tr>
    <td>Certain PWM</td>
    <td>0</td>
    <td>Move forward according to the input PWM</td>
  </tr>
  <tr>
    <td>0</td>
    <td>Certain PWM</td>
    <td>Move backward according to the input PWM</td>
  </tr>
  <tr>
    <td>0</td>
    <td>0</td>
    <td>Soft brake</td>
  </tr>
  <tr>
    <td>Max. PWM</td>
    <td>Max. PWM</td>
    <td>Hard brake</td>
  </tr>
</table>

You may have also noticed the checksum logic in our code. We are securing the commands using checksums. When the checksums don't match we know there has been a byte lost. Despite we have this algorithm we have almost never observed a checksum mismatch. Checksum security is a very easy security algorithm using the sum of the bytes with a `0xFF` mask. If the received bytes' sum filtered with the mask does not match the sent checksum, we can comfortably flag this package as unsafe.

```python
def send_command(value):
    data = value.to_bytes(4, 'big', signed=True)
    checksum = sum(data) & 0xFF # Value is checksummed
    if usb_serial.out_waiting < 64: # Send data if there is not much queue in usb storage
        usb_serial.write(data + bytes([checksum]))
```

Cruicial part about this function is limiting how much data is sent at any moment. We don't allow a queue of size more than `64 bytes`. This way usb does not get flooded. We actually did not have this logic at some point and we were losing connection between our motor driver.

We also send the checksum here. As discussed earlier it is for security reasons.

```python
while True:
    cmd = read_command()
    if cmd is not None: # If there is an incomming command
        servo_angle, motor_speed = cmd
        set_angle(servo_angle)
        move_motor(motor_speed)

    position = encoder.position
    if position != last_position:
        send_command(position)
        last_position = position

    time.sleep(0.001)
```

This is the main loop of the API. As you can see transmitting encoder values and receiving commands happen concurrently. You can view this API further in `src/pico.py`.

There is also another API inside of the Raspberry Pi to communicate with Raspberry Pi Pico. API for Raspberry Pi is almost identical to this code, and you can view it in `src/robot_car.py`.

> [!NOTE]
> Our motor driver API support motor commands at a frequency up to `50 Hz`, and we are using it at `20 Hz`. The limit for our usage is bound by our strategy and the overall logic for the solution.

### 2.2 Maintaining the direction

We would like to talk a little bit about how the robot goes straight. Gyro sensor is not reliable enough, and drifts very often. In theory, the gyro sensor we are using should drift only `1°` in `1 minute`. But unfortunately that is not the case. Reasons for this undeniable drift are the sharp turns; unpreventable electromagnetic waves coming from the lidar, motors and the battery; and an uneven center of mass.

We had two main ideas to fix this issue. If listed in chronological order they are:
- **Hit the wall**: After moving between sections we are making a `90°` turn. Our idea was to back up the robot to hit the wall, and after hitting the wall measure the gyro angle. This angle would give us the drift in the sensor. Although this method guarantees straightness both in theory and in practice (yes, we actually tried this method), issues with this solution are time and the risk of moving the walls. Hitting the wall with high speed is very risky as it might shatter the balance of the robot, so it should be down slowly, which is a disadvantage for time. Also moving the walls is against the rules, which is a risk not worth taking.
- **Add a numeric value to gyro**: We observed that the main drift in gyro accurs after making large turns. So we decided to add some constant angle to the gyro reading as we made those turns. For example after making the first turn into the second section we would add `+1` to whatever we read from the gyro. This method actually worked surprisingly well at first glance, but it also had problems. The constant value that we were adding to the gyro reading was not constant at all. We had to tune it every time, so this was another not working idea.

After having this unsuccessful ideas we realized that we could fix gyro drift using the lidar sensor. With a little bit geometry and drawing we observed this: if we take the closest point on the axis parallel to our robot, this point is always perpendicular to our robot. This information is valuable, becuase if a point is perpendicular to us, then it should be read as `90°` degrees in lidar values. But if it is not, then this means there is a drift in gyro because we are adjusting the lidar values with gyro. So it would reflect the error. This is the code for lidar reading and finding the gyro drift using lidar:

```python
def find_wall_tilt(self, scan):
    clos, perp = None, None
    for deg, dis in scan:
        var = (self.dir == 90 and deg <= -70) or (self.dir == -90 and \
                deg >= 70) # If a point is on the parallel axis.
        if var and (clos is None or dis <= clos): # If the point is closer than the previous one.
            clos, perp = dis, deg
    if perp is not None:
        if self.dir == 90:
            """
            Return the difference between the perpendicular angle and the
            angle we found the closest point in.
            """
            return -84.7 - perp
        elif self.dir == -90:
            return 90 - perp
    return None

def scan_callback(self, msg):
    gyro_angle = robot_car.read_gyro() # Read the gyro angle.
    all_scan, scan, rad = [], [], msg.angle_min
    for dis in msg.ranges:
        deg = gyro_angle - math.degrees(rad) # Adjust the lidar angle based on gyro angle.
        if math.isfinite(dis): # If the value is valid.
            if -95 <= deg <= 95:
                all_scan.append((deg, dis * 100))
            if -90 <= deg <= 90:
                scan.append((deg, dis * 100))
        rad += msg.angle_increment

    self.wall_tilt = self.find_wall_tilt(all_scan) # Find the wall tilt.
```

As you might have noticed we are using `-84.7°` for perpendicular angle instead of `-90°`. This is because of the offset in our lidar sensor. In a perfect lidar, this value would have been `-90°`. After finding the wall tilt we are subtracting the tilt from the gyro readings onward and this way we achive a straight-going robot.

>[!NOTE]
>We are not constantly calculating the wall tilt and adding it to gyro error. This wall tilt is only calculated when going between sections. The reson for this being that the axis paralel to the robot is clean at the intersection points of sections. If we tried to calculate the wall tilt mid-section, we could have mistakened a pillar to be the closest point and it would affect the gyro worse.

You can refer to the illustration below to get a better understanding of how this algorithm works. The while line is the perpendicular line connecting the point and the center of the robot. The arrow shows robot's initial heading, or what it refers to as `0°`. The green arc is showing how much the drift, or the error is. Although the arc in this illustration is very large, in real life the drift is in the range of `-4° to 4°`.

<div>
  Straighten Strategy
  <p style="margin-top:0;"><i>Figure 1.2: Straighten Strategy</i></p>
</div>

### 2.3 State Machines

A very important part of software is the state machine. The state machine is responsible for switching between the tasks our robot is executing. The tasks we generalized are:

```python
START = 0
KUBIK_UC = 1
KUBIK_TC = 2
BASE_WALL = 3
FOR_WALL = 4
NARROW = 5
FINAL = 6
```

These tasks are explained better in following sections, so they will not be explained here.

To maintain the structure we have two main variables `exec` and `waitin`. The variable `exec` means that whatever `exec` is set to should be executed immediately. And `waitin` means that a tick could be skipped before executing the task. They both have different use cases. For example:

```python
for_dis = robot_car.find(max, scan, -2.5, 2.5) # Front distance of the robot
if for_dis is not None and for_dis <= 30: # If it is very close and the robot needs to turn
    print('FOR_WALL prog')
    self.exec = FOR_WALL # Execute the task immediately
```

When a task is set to `exec`, robot does not react to any lidar data. Because it has a task to do and after finishing the task robot continues to read lidar data and switch between the tasks. But when it is set to `waitin`:

```python
"""
Some lidar calculations
"""
gyro_angle = robot_car.read_gyro()
scan, rad = [], msg.angle_min
for dis in msg.ranges:
    deg = math.degrees(rad) + 90
    if deg >= 180: deg -= 360
    deg = gyro_angle + deg
    dis *= 100
    if dis != 0 and math.isfinite(dis) and -130 <= deg <= 130 and dis >= 13:
        scan.append((deg, dis))
    rad += msg.angle_increment
scan.sort()

self.left_dis = robot_car.find(min, scan, -95, -85)
self.right_dis = robot_car.find(min, scan, 85, 95)
self.front_dis = robot_car.find(min, scan, -2.5, 2.5)

if self.waitin is not None: # If there is a task in the queue
    self.exec = self.waitin # Set it to be executed
    self.waitin = None # And reset the queue
```

As you can see in the tick we are skipping, we are actually reading lidar data and making calculations on it. This becomes especially handy when approaching the parking barriers. Robot needs to calculate their positions mid task, that's why the section for approaching them should run after the calculations.

### 2.4 Open Challange

Now let's continue with Open Challange overall logic. We have a very simple strategy for Open Challange: all we do is to go straight as much as we can, and when we get to close we make a turn. Let's take a look at some cruicial parts:

```python
gyro_angle = robot_car.read_gyro() # read the gyro angle from our robot_car api
scan, rad = [], msg.angle_min
for dis in msg.ranges:
    deg = gyro_angle - math.degrees(rad) # shift every angle by robot yaw
    if -90 <= deg <= 90 and math.isfinite(dis): # if an angle is valid
        scan.append((deg, dis * 100)) # add it to scan list
    rad += msg.angle_increment
```

As you can see from the code, we are shifting lidar angles by robot yaw. The reason for that is, we try to assume that angle `0°` is parallel to the outer wall. This is cruicial because we are making all detections and calculating wall distance according to lidar values. We also only take angles less than `90°` and greater than `-90°` because the back of our lidar is facing itself, and that data is not proprietary.

```python
if not self.f_dir: # if direction is not yet found
    forr_dis = robot_car.find(min, scan, -5, 5) # robot's front distance to outer wall
    if forr_dis is None or forr_dis > 100: # if front distance is too great
        gyro_angle = robot_car.read_gyro()
        gyro_error = -gyro_angle
        robot_car.move(head = gyro_error, speed = 40) # go straight following a straight line
    else: # if some distance is achieved
        left = robot_car.find(max, scan, -90, -10)
        right = robot_car.find(max, scan, 10, 90)
        if left is not None and (right is None or left > right): # if there is more to the left than to the right
            self.dir = -90 # movement direction is towards left
        else:
            self.dir = 90 # otherwise it is to right
        self.f_dir = True # now the direction is found and we can proceed
```

We detect movement direction by detecting if there is a greater gap to the left of the robot than the right of the robot, and vice versa. The reason why we don't do it directly at the start is because robot's front could be placed far away from the outer wall. In this case robot can't really determine which side is more emptier, because the inner walls are not allowing it to.

```python
accel_speed = robot_car.calc_ccel(30, 60, 300 - for_dis, 70) # calculate acceleration according to front distance
if self.count == 12: # go slower if this is the last section
    deaccel_speed = robot_car.calc_ccel(30, 30, for_dis, 300)
else: # other deaccelerate a little bit lighter
    deaccel_speed = robot_car.calc_ccel(30, 60, for_dis, 130)
self.idle_speed = min(accel_speed, deaccel_speed) # we go with minimum value among both
```

At every point we calculate acceleration and deacceleration values. We go as fast as the minimum of them, this creates an effect of speeding up, then going steady and then slowing down. Slowing down when getting closer helps us to make turns more accurate as we have more space to make a turn. When approaching the outer wall fast, the turning algorithm might be triggered later than it should because of the low frequency of our lidar. And speeding slowly up after turns make our robot go more straight considering slow speed bumps make robot slip from the ground less.

```python
if self.count == 12 and forr_dis is not None and forr_dis <= 180: # if it is last section and some distance is achieved
    robot_car.move(0, 0) # soft brake
    robot_car.ser.close() # close the communication with motor driver
    raise Exception # end the opmode
```

This is a pretty basic terminal code which end the opmode when it is the last section of the run and some distance is achieved. You can see the illustration to get a better idea of our open runs:

<div>
  Straighten Strategy
  <p style="margin-top:0;"><i>Figure 1.3: Open Challange Strategy</i></p>
</div>

### 2.5 Obstacle Challange

#### 2.5.1 Skews

Before starting to talk about how we are solving the obstacle challange it is important to talk about the skew. Our robot always maintains an orientation paralel to the outer walls, so when surpassing a pillar we need some special technique. After making some research and observations on real cars, we stumbled upon what we call "skew".

The main objective for a skew mechanic is when a pillars' color is identified and we know which side we should pass from, we first drive in that direction for certain amount. After reaching that amount, we steer the opposing direction and try to get the robot parallel to the outer walls again.

<div>
  Skew
  <p style="margin-top:0;"><i>Figure 1.4: Skew</i></p>
</div>

"The certain amount robot steers in correct direction" is achieved using the gyroscope sensor. This means that robot steers in the direction while some angle is not achieved. Calculating this angle is tricky, but when you know the relation between the distance you want to skew and the heading angle to achive, it is more approachable to estimate this value.

We first assumed that the relation was linear, but we very soon realized it was incorrect. Robot was moving very on-point for close distances, but when they got larger, robot started to either overshoot or undershoot. Then we realized that the relation was radical and involving the square root. The formula we designed to fit the angle is:

$$\large Heading_{\text{skew}} = K_{\text{skew}} \times \sqrt{X_{\text{dis}}} + B_{\text{skew}}$$

In this formula $$Heading_{\text{skew}}$$ is the output of the formula, which is how much heading the robot needs to achive before trying to fix itself to be parallel. $$K_{\text{skew}}$$ and $$B_{\text{skew}}$$ are the constants. We need those, as square root is only indicating the relation. To fit this relation to our robot and real world environment we need to justify the output. $$X_{\text{dis}}$$ is how much distance robot wants to achive in x-axis. Using this method we can make the robot move a certain x-axis distance.

But when passing pillars it is at least as important to calculate how much distance should be skewed. To calculate this distance, we take the robot's distance to the pillar we are trying to skew to. And when surpassing a pillar, we try to surpass in a safe distance. We calculate that this according to these formulas:

$$\large Distance_{\color{green}green} = -\frac{Pillar_{\text{pos}}}{2} \quad \large ; \quad \large Distance_{\color{red}red} = \frac{100 - Pillar_{\text{pos}}}{2}$$

Here, $$Pillar_{\text{pos}}$$ indicates the pillar's distance from the outer wall. Among these formulas we use the one according to the pillar's color. This formulas only work for clockwise direction. For counterclockwise they are like this:

$$\large Distance_{\color{green}green} = \frac{Pillar_{\text{pos}}}{2} \quad \large ; \quad \large Distance_{\color{red}red} = -\frac{100 - Pillar_{\text{pos}}}{2}$$

As you can see the formulas become the inverse.

#### 2.5.2 Color Detection

Color detection is done using HSV values. Color detection using HSV values is pretty standart and works in this principle:
- You specify 3 values (Hue, Saturation, and Value) spectrum (min. and max. values).
- Then create a mask in this spectrum (mask is some kind of a filter, like the ones used in social medias).
- Apply the mask to the retrieved image.
Colors that don't match the filter will have the value zero. So every value that is not zero is matching the color filter. Using this property we used this kind of an algorithm:

```python
def find_colors(self, hsv, colors): # Try to match every color's filter in the list colors
    area = dict() # Store the areas of each color filter's match
    for color, codes in self.colors.items():
        if color in colors:
            area[color], mask = 0, None # Initialize the values to zero
            for code in codes:
                color_low = numpy.array(code[0])
                color_high = numpy.array(code[1])
                m = cv2.inRange(hsv, color_low, color_high)
                mask = m if mask is None else cv2.bitwise_or(mask, m) # Bitwise or all the masks belonging to the same color
            if mask is not None:
                coords = cv2.findNonZero(mask) # Find all non zeros
                if coords is not None:
                    area[color] = len(coords) # The length is equal to the area of the color in the frame
    return area

def camera_callback(self, msg):
    np_arr = numpy.frombuffer(msg.data, numpy.uint8) # Convert ROS message into a numpy array
    frame = cv2.imdecode(np_arr, cv2.IMREAD_COLOR) # Convert the numpy array into an opencv frame
    height, width, _ = frame.shape
    hsv = cv2.cvtColor(frame, cv2.COLOR_BGR2HSV) # Convert the color values into HSV spectrum
    k_hsv = hsv[height*4//10:,:] # We only take lower 60% of the frame (explained below)
    k_area = self.find_colors(k_hsv, ('green', 'red')) # We only check for colors green and red
    if k_area['green'] > k_area['red']: self.color = GREEN # If green's are is more anything in front is assumed to be green
    elif k_area['red'] > k_area['green']: self.color = RED # Otherwise it is considered red
    else: self.color = None # If no pixels match, there is no color
```

As you can see in our implementation robot is bitwise oring multiple color masks (filters). The reason for this is we figured out we can not fit every pixel of the pillar under some lightings. That's why we get multiple spectrums and combine them. Whichever ligthing is happening (dark or light), the robot does not get affected by it. These are some values we used in national finals (we almost never changed them eversince):

```python
self.colors = {
    'green': [((70, 128, 75), (86, 255, 170)), ((67, 106, 22), (78, 188, 182)), ((69, 51, 33), (95, 193, 154)), ((59, 93, 58), (79, 229, 147)), ((18, 27, 88), (97, 188, 156))],
    'red': [((0, 154, 160), (179, 206, 235)), ((0, 113, 0), (8, 255, 255)), ((0, 40, 124), (1, 219, 196)), ((170, 76, 159), (180, 255, 215))],
}
```

The values here are in the format of minimum and maximum value pairs of HSV values (Hue, Saturation, and Value). The reason why we only take the lower `60%` of the frame is: if we take the whole frame there can be 2 pillars seen in the same frame. This way robot might assume that the next pillar is the one it is seing right now. That's why we limit the robot's view by only bottom `60%`. We also tilt the physical camera for the same exact reason.

#### 2.5.3 Main Strategy

Now let's talk about the famous Obstacle Challange! *Everyone is so excited!* We break the obstacle challenge into wro subchallanges:

<ol>
  <li><b>UC</b> (Untraced Cubes): In this section, we assume (and we actually do) that we don't know colors of any pillars. Because of this reason we first approach to each pillar and try to identify its color. Only after identifying its color we either surpass it on the right or the left. We also save the color of the pillar for later.</li>
  <li><b>TC</b> (Traced Cubes): In this section we assume (yet we do) know every pillar's color. So only thing left to do is just surpass it from the correct side. We read every pillar's color from the list and behave accordingly. After surpassing every cube we increment the pointer by one and assume that next pillar will have the next color in the list.</li>
</ol>

As you may have noticed we can do TC rounds twice as we only need to see each pillar once to know its color. We find it very interesting that TC rounds are twice as fast than UC rounds. UC rounds take `70 s` in average and TC rounds only take approximately `30 s`. We also speed things up a little bit when doing TC rounds, because we no longer need high precision when detecting the pillars, even if they are detected late we still have enough reaction time to surpass it on the correct side.

Let's look at the code which determins the round to be executed:

```python
kubik = self.find_kubik(scan, r_wall_dis) # this is a method which finds kubik's position

if kubik is not None and self.on_this_side < 2: # if there is at least one pillar yet to be seen
    self.kubik = kubik
    if self.count < 5: # if we are still on first lap
        print('KUBIK_UC prog')
        self.exec = KUBIK_UC # it is a UC round because we have not memorized all colors yet
        self.on_this_side += 1
    else: # otherwise if it is second or third lap
        side, y_dis = self.kubik
        var = self.dir == 90 and (self.last_side is None or side != self.last_side)
        if self.last_dis is None or (y_dis > self.last_dis and not abs(y_dis - self.last_dis) < 2) or var:
            self.kubik_ix = (self.kubik_ix + 1) % len(self.kubiks) # we increase the pointer by one
            if self.seen_start and self.kubik_ix == len(self.kubiks) - 2:
                self.lap_cnt += 1
            elif not self.seen_start and self.kubik_ix == len(self.kubiks) - 1:
                self.lap_cnt += 1
            self.last_side = side
            self.exec = KUBIK_TC
            print('KUBIK_TC prog', self.last_dis)
            self.on_this_side += 1
        self.last_dis = y_dis
```

As you may see we have more checks on pillars when executing TC rounds. That is because, with high speed there is a greater chance of error. The checks we are doing here are sufficient enough to avoid false positives. The main checks we are doing are:
- If the pillar side (left or right, based on distance to the wall which is always either `40 cm` or `60 cm`) does not match with the memorized pillar side;
- If the pillar detected now is closer than the previously detected pillar (we keep track of the pillar distance as we approach it, if it gets less or remains the same it means the robot is detecting the same pillar over again).

```python
def find_kubik(self, data, wall_dis):
    """
    A pillar is detected using two points only: the closest one,
    and the furthest one. If the distance between them is greater than
    some threshhold it means there is some object in sight which is
    further away than the front outer wall. This can either be an inner
    wall or the pillar. To avoid the inner wall case, we limit the
    relative x distance from paralel outer wall. This way the closest
    point can only be a pillar.
    """

    if wall_dis is None: # if lidar values are unsificient
        return None # there can't be any pillars detected

    # limits for relative distance from the outer wall
    left_lim = self.off_x - wall_dis
    right_lim = 100 - self.off_x - wall_dis

    if self.dir == -90: # they switch up if going counterclockwise
        left_lim, right_lim = -right_lim, -left_lim

    closest, furthest = None, None

    for point in data:
        y_dis, x_dis = self.find_katets(point)
        if left_lim <= x_dis <= right_lim:
            if closest is None or closest[0] > y_dis:
                closest = (y_dis, x_dis)
            if furthest is None or furthest[0] < y_dis:
                furthest = (y_dis, x_dis)

    var = closest is not None and ((self.dir == 90 and closest[0] >= 100) or (self.dir == -90 and closest[0] >= 100))

    # if any unsificient data, or if closest point is too close to the furthest point
    if closest is None or furthest is None or \
            furthest[0] - closest[0] <= 60 or \
            var or closest[0] <= 15:
        return None

    # calculate pillar's relative distance to the parallel outer wall
    if self.dir == 90:
        from_wall_dis = wall_dis + closest[1]
    elif self.dir == -90:
        from_wall_dis = wall_dis - closest[1]

    if (self.dir == 90 and from_wall_dis <= 50) or (self.dir == -90 and from_wall_dis <= 43):
        return 40, closest[0] # it is on the left side, with y distance closest[0]
    else:
        return 60, closest[0] # it is the right side, with y distance closest[0]
```

We have designed this algorithm after many unsuccessful iterations. But this one was pretty efficient. It has a time complexity of `O(N)` with a pretty low constant coefficient. We would like to share a previous idea we had:

Cluster the points according their distance with each other. If there is a group with a diameter of at most `~8 cm` (`√(5²+5²)`) it is a pillar. This method worked poorly, because clustering the points according their distance took `O(N²)` complexity as we looked at each pair of them. To optimize this method we used an algorithm so called DSU (Disjoing Set Union). Using this technique it is possible to cluster `N` points with almost linear time complexity (with an inverse ackermann coefficient). Even after optimizing this method, we discovered that our lidar does not give precise enough data to use this method.

Thankfully, we switched to our current approach and did not think much to fix the previous one.

#### 2.5.4 Parallel Parking

Parallel parking is a tricky challange considering its need for high-precision. With all the algorithms explained above we were able to achieve this precision. Now the main challange was the robot's dimensions. Our robot had a width of whopping `17cm`. This means we only had a margin of error of only `3cm`. Actually, hitting the wall while parking was also a risk so the margin of error should be calculated from both ends which means the error of margin was just `1.5cm` from both sides. To achieve a better performance, in our new robot we reduced the width of the robot to `15cm`. Which added a centimeter to our margin of error, which is actually a decent difference.

Our method for parallel parking is like this:
- If there isn't a pillar at the final section we just execute the method for green pillar scenario.
- If the last pillar is green, we skew close to the parking lot, then robot moves to reach the furthest parking barrier. Afterwards robot does an inverse left turn. Then we fix the steering to right and move in.
- If the last pillar is red, we surpass the red pillar, make an inverse left turn and then back up while the parking lot is far. After we reach some distance, we do a right turn. This is for increasing the turning arc for inverse right turn. After doing this we make the inverse right turn and finish the parallel parking.

We have a special algorithm to find where the parking barriers are.

```python
def find_park(self, scan):
    """
    These variables are for:
        - ly1: The last y coordinate for a parking barrier candidate.
        - lx1: First x coordinate for a parking barrier candidate.
        - lx2: Last x coordinate for a parking barrier candidate.
    """
    ly1, lx1, lx2 = None, None, None
    for p in scan:
        if p[0] < -85 or p[0] > 30: # Parking appears only in certain angles
            continue
        """
        Here we convert the polar pairs to cartesian coordinates.
        """
        y_dis = abs(p[1] * math.sin(math.radians(90 + p[0])))
        x_dis = abs(p[1] * math.cos(math.radians(90 + p[0])))
        """
        Algorithm is such:
            - If the difference between y distances is greater than 3 (the parking barriers' have a width of 2) we know we either have the parking lot inside of the range or not.
            - If the difference between the first and last x coordinates in this windows is greater than 5 (parking barriers' length is 20) we know it is a parking barrier.
            - Otherwise we continue to look for a parking barrier.
        """
        if ly1 is None or abs(y_dis - ly1) > 3:
            if lx2 is not None and abs(lx2 - lx1) > 5:
                return (lx2, ly1)
            ly1, lx1, lx2 = y_dis, x_dis, x_dis
        else:
            lx2 = x_dis
    return None # If no parking barrier is found we return None.
```

This algorithm returns the closest parking barrier. This information is very handy, because we always need approaching to parking barriers. To approach the parking barriers:

```python
if self.dis_till is None: # If parking barrier's location is yet to be calculated
    park = self.find_park(scan) # Find the location
    self.dis_till = park # And set it to the variable
if self.dis_till is not None: # If parking barrier's location has been calculated
    if self.start_pos is None and robot_car.pos is not None: # If start position of encoder is not retrieved
        self.start_pos = robot_car.pos # Give the appropriate value
    if robot_car.pos is None or robot_car.rot_to_cm(robot_car.pos - self.start_pos) < self.dis_till[1] + \
            dis_arr[self.mov_park]: # Move until calculated distance is not achieved by the robot
        err = -robot_car.read_gyro()
        robot_car.move(err * 5, 17) # Move by constant speed using P steering
    else:
        robot_car.hard_brake() # Finish
```

>[!NOTE]
>This is not the full code snippet. Some parts have been cut off because they have no direct relation with approaching the barrier algorithm.

# 3. Development Environment

Let's get into setting up the development environment. We have a very generic development environment for the host machine. The only programs you need to develop is `ssh` and any text editor of your choice. All of the modern machines nowadays come with these by default. To develop on the host machine we used `Command Prompt` in our Windows machine and `Terminal` in our Ubuntu machine.

Environment for the Raspberry Pi is a little bit more complex but to make it simpler we developed a solution as such:



This is our Raspberry Pi image. If you flash this file into your Raspberry, you will get the exactly same environment as us. To flash this image you can use ``Rufus`` for Windows, ``UNetbootin`` for Linux or ``WonderISO`` for MacOS.

<div>
  Rufus
  <p style="margin-top:0;"><i>Figure 1.5: Rufus flashing tool</i></p>
</div>

But if you want to customize installation you should flush the Raspberry Pi from the official Raspberry Pi Imager. If not, just skip to the `Code and Strategy` section.

> [!WARNING]
> To be able to execute the commands and instructions below you need a microSD card of at least `16GB` storage. The operating system for Raspberry Pi will be installed in this microSD card. If you have any important files in the microSD card, please back them up because after the installation they will be erased from the card.

We are using `Ubuntu Server 24.04.3 LTS (64-bit)` for our Raspberry Pi. You can install this OS to your microSD as you want, but the recommended way is to use the official [Raspberry PI Imager tool](https://www.raspberrypi.com/software/).

<div>
  Raspberry Pi Imager
  <p style="margin-top:0;"><i>Figure 1.6: Raspberry Pi Imager</i></p>
</div>

After selection your Raspberry Pi model press "Choose OS". Afterwards select the `Other general-purpose OS` > `Ubuntu` > `Ubuntu Server 24.04.3 LTS (64-bit)` operating system.

<div>
  Ubuntu Server 24.04.3 LTS (64-bit)
  <p style="margin-top:0;"><i>Figure 1.7: Ubuntu Server 24.04.3 LTS (64-bit)</i></p>
</div>

> [!NOTE]
> `Ubuntu Server 24.04.3 LTS (64-bit)` is the latest release for Ubuntu Server. Despite this, it support many Raspberry Pi versions. Without the loss of generality, you do not need to install this specific version of Ubuntu to be able to execute the instructions and commands, but it is recommended as it is what we used.

> [!NOTE]
> It is not possible to use `Raspberry Pi OS (Raspbian)` for this project. The reason for that is `ROS2 JAZZY`, a dependency for this project, not being supported by `Raspbian`. There might be some workarounds to get it to work, but it would be a waste of time as `Ubuntu Server 24.04.3 LTS (64-bit)` is already as minimal as official `Raspbian`.

Now to configure the operating system press `Ctrl` `Shift` `X` or `⌘` `Shift` `X`. In the panel that opened, under the `General` tab set your internet settings and your credentials for Raspberry Pi user. After that switch to `Services` tab and enable `SSH` and `Password Authentication`. After doing all the configurations press `Next` and the installation will start.

After the installation is complete plug the microSD card into Raspberry Pi. After it boots, it is recommended to execute following commands:

```
$ sudo apt update
$ sudo apt upgrade
```

After installing the operating system you can install the ROS2 environment.

Start with installing `Git`. This package will be used for installing other packages from the internet:

```bash
$ sudo apt-get install git
```

To be able to use Raspberry Pi camera module, the packages `libcamera` and `rpicam-apps` should be installed. Start with installing the dependencies:

```bash
$ sudo apt install -y libboost-dev
$ sudo apt install -y libgnutls28-dev openssl libtiff5-dev pybind11-dev
$ sudo apt install -y meson cmake
$ sudo apt install -y python3-yaml python3-ply
$ sudo apt install -y libglib2.0-dev libgstreamer-plugins-base1.0-dev
```

And now to install the package:

```bash
$ git clone https://github.com/raspberrypi/libcamera.git
```

Go to the root directory:

```bash
$ cd libcamera
```

To configure the package build:

```bash
$ meson setup build --buildtype=release -Dpipelines=rpi/vc4,rpi/pisp -Dipas=rpi/vc4,rpi/pisp -Dv4l2=true -Dgstreamer=enabled -Dtest=false -Dlc-compliance=disabled -Dcam=disabled -Dqcam=disabled -Ddocumentation=disabled -Dpycamera=enabled
```

And finally to install `libcamera` package:

```bash
$ sudo ninja -C build install
```

After installing `libcamera` package we can install `rpicam-apps`. Start with dependencies:

```bash
$ sudo apt install -y cmake libboost-program-options-dev libdrm-dev libexif-dev
$ sudo apt install -y meson ninja-build
```

Go to the root directory and download the package:

```bash
$ git clone https://github.com/raspberrypi/rpicam-apps.git
```

Move to the package directory:

```bash
$ cd rpicam-apps
```

Before doing the configuration install `libav` package to be able to record videos using the camera:

```bash
$ sudo apt install -y libavcodec-dev libavformat-dev libavutil-dev libswscale-dev libavdevice-dev libavfilter-dev
```

Now you can configure the build:

```bash
$ meson setup build -Denable_libav=enabled -Denable_drm=enabled -Denable_egl=disabled -Denable_qt=disabled -Denable_opencv=disabled -Denable_tflite=disabled -Denable_hailo=disabled
```

And finally install `rpicam-apps`:

```bash
$ meson compile -C build
$ sudo meson install -C build
```

You should end the installation with updating the `ldconfig cache`. This is handy for using the installed packages in other directories:

```bash
$ sudo ldconfig
```

Now that all the required packages are installed we can install `ROS2 Jazzy` integration.

[`ROS2 Jazzy`](https://docs.ros.org/en/jazzy/index.html) is a collection of robot integration packages. With the following instructions you should be able to get `ROS2 Jazzy` on your system.

Configure the locale for Raspberry Pi:

```bash
$ locale 
$ sudo apt update && sudo apt install locales
$ sudo locale-gen en_US en_US.UTF-8
$ sudo update-locale LC_ALL=en_US.UTF-8 LANG=en_US.UTF-8
$ export LANG=en_US.UTF-8
$ locale 
```

Add required repositories to the `apt` package manager to be able to install required apps:

```bash
$ sudo apt install software-properties-common
$ sudo add-apt-repository universe
```

Now add `ros2-apt-source` package:

```bash
$ sudo apt update && sudo apt install curl -y
$ export ROS_APT_SOURCE_VERSION=$(curl -s https://api.github.com/repos/ros-infrastructure/ros-apt-source/releases/latest | grep -F "tag_name" | awk -F\" '{print $4}')
$ curl -L -o /tmp/ros2-apt-source.deb "https://github.com/ros-infrastructure/ros-apt-source/releases/download/${ROS_APT_SOURCE_VERSION}/ros2-apt-source_${ROS_APT_SOURCE_VERSION}.$(. /etc/os-release && echo $VERSION_CODENAME)_all.deb" # If using Ubuntu derivates use $UBUNTU_CODENAME
$ sudo dpkg -i /tmp/ros2-apt-source.deb
```

To enable the programming environment:

```bash
$ sudo apt update && sudo apt install -y \
  python3-flake8-blind-except \
  python3-flake8-class-newline \
  python3-flake8-deprecated \
  python3-mypy \
  python3-pip \
  python3-pytest \
  python3-pytest-cov \
  python3-pytest-mock \
  python3-pytest-repeat \
  python3-pytest-rerunfailures \
  python3-pytest-runner \
  python3-pytest-timeout \
  ros-dev-tools
```

Now create a `ROS2 Jazzy` workspace and install required `ROS2 Jazzy` packages:

```bash
$ mkdir -p ~/ros2_jazzy/src
$ cd ~/ros2_jazzy
$ vcs import --input https://raw.githubusercontent.com/ros2/ros2/jazzy/ros2.repos src
```

To be confident that all the packages are up-to-date:

```bash
$ sudo apt upgrade
```

Finally install everything:

```bash
$ sudo rosdep init
$ rosdep update
$ rosdep install --from-paths src --ignore-src -y --skip-keys "fastcdr rti-connext-dds-6.0.1 urdfdom_headers"
```

After installing the `ROS2 Jazzy` system we can install required packages for the project.

Installing `ROS2 Jazzy` system is not enough to use it. You need to source `/opt/ros/jazzy/setup.bash` everytime you want to use it. If you don't want to explicitely do it everytime execute this command, which add the command to startup:

```bash
$ echo "source /opt/ros/jazzy/setup.bash">>~/.bashrc
```

After executing the command restart the console.

`camera_ros` is a package to integrate camera with `ROS2 Jazzy`. To install `camera_ros` execute the following commands:

```bash
$ cd ~/ros2_jazzy/src
$ sudo apt -y install python3-colcon-meson
$ git clone https://github.com/christianrauch/camera_ros.git
$ source /opt/ros/$ROS_DISTRO/setup.bash
$ cd ~/ros2_jazzy/
$ rosdep install -y --from-paths src --ignore-src --rosdistro $ROS_DISTRO --skip-keys=libcamera
$ colcon build --event-handlers=console_direct+
```

`rplidar_ros` is a package to use RPLidar system. To install it:

```bash
$ cd ~/ros2_jazzy/src
$ git clone https://github.com/Slamtec/rplidar_ros.git
$ rosdep install -y --from-paths src --ignore-src --rosdistro $ROS_DISTRO --skip-keys=libcamera
$ colcon build --symlink-install
```

To use the packages after installing them you should source `~/ros2_jazzy/install/setup.bash` everytime. If you don't want to add it to the `~/.bashrc`:

```bash
$ echo "source ~/ros2_jazzy/install/setup.bash">>~/.bashrc
```

# 4. Downloading our source code

Downloading the source code is very straight forward. There are two options:
1. Download the source code as a zip from our GitHub repository and then move the file into Raspberry Pi using `scp` command line tool (WinSCP if you prefer GUI instead).
2. Download directly inside the Raspberry Pi using `git` (the installation proccess of git is shown in the above step).

We will focus on the second step as it is more trivial. To download the source code connect to your Raspberry Pi and type in this command:

```bash
git clone https://github.com/coolboy19521/AZE44.git
```

Now you have installed the source code and the schemes, models etc. If you just want to install the code, instead of the command above use these commands:

```bash
git clone --no-checkout https://github.com/coolboy19521/AZE44.git cd AZE44
git sparse-checkout init --cone
git sparse-checkout set src
git checkout main
```

This way you only install the `src` directory. After installing the source code to navigate to it use:

```bash
cd ~/AZE44/src
ls
```

After writing these commands you should see an output like this:

```bash
calibrate_skew.py obstacle.py open.py pico.py README.md robot_car.py
```

These files include the implementations of functionalities described above in the documentation. The rough description for each of them is like this:
- `calibrate_skew.py`: This file is for calibrating the skew mechanic. Program inputs you for a number and depending on the constants performs a skew. To change the constants you can edit the file via your favorite text editor (i.e. `vim` or `nano`). The constants you should change are `A` and `B`. For best calibration it is adviced to fit these variables for `10cm` skews and then for `30cm` skews.
- `obstacle.py`: This file includes our solution for Obstacle Challange.
- `open.py`: Similarly, this file includes our solution for Open Challange.
- `pico.py`: This is our motor driver code. If you decide to use different motor drivers or servos with different working principles, you can just modify the `move_motor` and `set_angle` functions inside this code. All the other stuff should work for any hardware (if you are still using a Pico).
- `README.md`: This file is the software documentation. You can delete it if you don't need, but keeping it might guide you on our software.
- `robot_car.py`: This file contains our API for interfacing the Raspberry Pico motor driver. You don't need to modify this code at all, because it is just sending commands unrelated to the hardware being used.

<hr>

<p align="center">
  <picture>
  <source media="(prefers-color-scheme: dark)" srcset="../media/my_image.png">
  
  </picture>
</p>

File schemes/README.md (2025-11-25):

# 1. Bill of Materials (BOM)

<table align="center">
  <tr>
    <th colspan="4">Electronics</th>
  </tr>

  <tr>
    <th>Component</th><th>Picture</th>
    <th>Component</th><th>Picture</th>
  </tr>

  <tr>
    <td>Raspberry Pi 5 x 1</td><td></td>
    <td>Motor Driver x 1</td><td></td>
  </tr>

  <tr>
    <td>T-MINI-Plus Lidar TOF</td><td></td>
    <td>BNO085 x 1</td><td></td>
  </tr>

  <tr>
    <td>3s Li-Po x 1</td><td></td>
    <td>IMAX B6AC battery charger x 1</td><td></td>
  </tr>

  <tr>
    <td>Servo Motor TD8120MG x 1</td><td></td>
    <td>Raspberry Pi Camera Module 3 x 1</td><td></td>
  </tr>

  <tr>
    <td>Encoder motor x 1</td><td></td>
    <td>Switch ON-OFF x 1</td><td></td>
  </tr>

  <tr>
    <td>2,54 mm JST-XH Connector Male x 5</td><td></td>
    <td>2,54 mm JST-XH Connector Female x 5</td><td></td>
  </tr>

  <tr>
    <td>XT-60 x 1</td><td></td>
    <td>2.54 mm Pin Header x 1</td><td></td>
  </tr>

  <tr>
    <td>Fuse x 1</td><td></td>
    <td>10K ohm resistor x 1</td><td></td>
  </tr>

  <tr>
    <td>330ohm resistor x 2</td><td></td>
    <td>GPIO cable x 1</td><td></td>
  </tr>

  <tr>
    <td>Li-Po Battery Test Device Amper Monitor x 1</td><td></td>
    <td>Type-c - Type-c Kabel x 1</td><td></td>
  </tr>

  <tr>
    <td>32 GB Storage Card x 1</td><td></td>
    <td>Heat sink x 1</td><td></td>
  </tr>

  <tr>
    <td>HC-SR04 x 1</td><td></td>
  </tr>
</table>

# 2. System Overview

### 2.1 Electronic System Architecture

**Raspberry Pi 5 (Main Controller):** The central processing unit
running the ROS-based software. It collects data from all sensors and
generates motor and servo commands.

**Raspberry Pi Pico 2 (Motor Controller):** Controls the encoder motor
and servo motor. It converts commands from the Raspberry Pi into
motor/servo movements and sends feedback data back to the Pi.

**Encoder DC Motor:** Provides forward and backward motion. Through the
encoder, it sends speed and position feedback to the Raspberry Pi via
the Motor Controller.

**Servo Motor:** Handles robot turns, with the servo angle controlled
via the motor controller.

<div>
  Diagram
  <p style="margin-top:0;"><i>Figure 1.1 Flow Diagram</i></p>
</div>

# 3. Hardware and Component Introduction

### 3.1 Raspberry Pi 5

#### 3.1.1 Description and Features

<table align="center" style="width:80%; border-collapse:collapse;">
  <tr>
    <th colspan="3">Raspberry Pi 5</th>
  </tr>
  <tr>
    <td rowspan="3" style="width:400; text-align:center; vertical-align:middle; padding:0; margin:0;">
    <div>
      Raspberry Pi
      <p style="margin-top:0;" align="left"><i>Figure 2.1: Raspberry Pi 5</i></p>
    </div>
    </td>
    <td>USB</td>
    <td>Raspberry Pi Pico W and T-MINI-PLUS Lidar sensor</td>
  </tr>
  <tr>
    <td>CSI Camera Port</td>
    <td>Connects to Camera Module 3</td>
  </tr>
  <tr>
    <td>GPIO Pins</td>
    <td>Start button, imu, ultrasonic, leds and buzzer</td>
  </tr>
  <tr>
    <td colspan="3">Quad-core CPU, 64-bit @ 2.4 GHz, 8 GB RAM</td>
  </tr>
  <tr>
    <td colspan="3">2 × USB 3.0, 2 × USB 2.0 ports</td>
  </tr>
  <tr>
    <td colspan="3">40-pin GPIO header</td>
  </tr>
  <tr>
    <td colspan="3">USB-C power input 5V/5A</td>
  </tr>
  <tr>
    <td colspan="3">Powered by Li-Po 3S 1300 mAh battery</td>
  </tr>
</table>

Raspberry Pi 5 is a high-performance single-board computer used as
the main controller of the robot. Its purpose in our robot is:
- Gather lidar, camera, gyro, and encoder data. All of our sensors are connected to Raspberry Pi.
- Proccess the data gathered and make decisions. It could be some kind of a brain, if sensors could be considered as the sense organs.
- Send the decisions made to Raspberry Pi Pico. Raspberry Pi is connected to Raspberry Pi Pico via USB. More information about these kind of connections could be found in [`3.9.7 Scheme 1`](#control-board).

#### 3.1.2 Connections and Pin Configuration

<div>
  Raspberry Pi Pinout
  <p style="margin-top:0;"><i>Figure 2.2: Raspberry Pi Pinout</i></p>
</div>

>[!NOTE]
>Refer to the Raspberry Pi 5 pinout for accurate connections. If you want to see connection diagram, you need to go to [`3.9.7 Scheme 1`](#control-board).

### 3.2 Raspberry Pi Pico W Control Board

#### 3.2.1 Description and Features

<table align="center" style="width:80%; border-collapse:collapse;">
  <tr>
    <th colspan="3">Raspberry Pi Pico 2 W</th>
  </tr>
  <tr>
    <td rowspan="3" style="width:400; text-align:center; vertical-align:middle; padding:0; margin:0;">
    <div>
      Raspberry Pi Pico
      <p style="margin-top:0;" align="left"><i>Figure 3.1: Raspberry Pi Pico 2 W</i></p>
    </div>
    </td>
    <td>Wireless Connectivity</td>
    <td>2.4 GHz Wi-Fi</td>
  </tr>
  <tr>
    <td>Communication Interfaces</td>
    <td>USB, UART, I²C, SPI, PWM, ADC</td>
  </tr>
  <tr>
    <td>GPIO Pins</td>
    <td>26 multifunctional pins</td>
  </tr>
  <tr>
    <td colspan="3">RP2350 microcontroller, Dual-core ARM (up to 150 MHz)</td>
  </tr>
  <tr>
    <td colspan="3">USB 5 V input, regulated 3.3 V output (maximum 300 mA)</td>
  </tr>
  <tr>
    <td colspan="3">520 KB SRAM, 4 MB Flash</td>
  </tr>
</table>

**Raspberry Pi Pico W** is a compact and efficient microcontroller board designed for real-time embedded control, IoT, and robotic applications. It features a dual-core ARM Cortex-M0+ processor, integrated Wi-Fi connectivity, and flexible GPIO pins supporting multiple communication and control interfaces. Its purpose in our robot is:
- Read encoder sensor and send them to Raspberry Pi. Encoder sensors are connected to Raspberry Pi Pico. More information on this could be found in [`3.9.7 Scheme 1`](#control-board).
- Read motor command values from Raspberry Pi and send them to motor driver. Motor drivers are connected to Raspberry Pi Pico but the decisions are made in Raspberry Pi. That's why Raspberry Pi Pico should read the decisions from the Raspberry Pi.

#### 3.2.2 Connections and Pin Configuration

<div>
  Raspberry Pi Pico 2 Pinout
  <p style="margin-top:0;"><i>Figure 3.2: Raspberry Pi Pico 2 Pinout</i></p>
</div>

>[!NOTE]
>Refer to the Raspberry Pi Pico W pinout for accurate connections.  If you want to see connection diagram, you need to go to [`3.9.7 Scheme 2`](#motor-driver).

### 3.3 TB6612FNG Control Board

#### 3.3.1 Description and Features

<table align="center" style="width:80%; border-collapse:collapse;">
  <tr>
    <th colspan="3">TB6612FNG</th>
  </tr>
  <tr>
    <td rowspan="3" style="height:300px; text-align:center; vertical-align:middle; padding:0; margin:0;">
    <div>
      TB6612FNG
      <p style="margin-top:0;" align="left"><i>Figure 4.1: TB6612FNG</i></p>
    </div>
    </td>
    <td>Operating voltage</td>
    <td>2.5V – 13.5V</td>
  </tr>
  <tr>
    <td>Continuous output current</td>
    <td>1.2A per channel (peak up to 3.2A)</td>
  </tr>
  <tr>
    <td>Logic voltage</td>
    <td>2.7V – 5.5V</td>
  </tr>
  <tr>
    <td colspan="3">Dual H-Bridge motor driver (can control 2 DC motors)</td>
  </tr>
  <tr>
    <td colspan="3">PWM control supported (up to 100 kHz)</td>
  </tr>
</table>

#### 3.3.2 Connections and Pin Configuration

<div>
  TB6612FNG Pinout
  <p style="margin-top:0;"><i>Figure 4.2: TB6612FNG Pinout</i></p>
</div>

## 3.4 Motors and Servo Motor

### 3.4.1 Powering and Controlling

**DC Motor:**
- Connected to Raspberry Pi Pico W via encoder motor ports.
- Encoder feedback allows precise speed and position control.
- Controlled using PWM signals.

**Servo Motor:**
- Controlled via PWM from Raspberry Pi Pico W 

### 3.4.2 DC Gear Motors

#### 3.4.2.1 Description and Features

<table align="center" style="width:80%; border-collapse:collapse;">
  <tr>
    <th colspan="3">Gear Motor</th>
  </tr>
  <tr>
    <td rowspan="3" style="height:350px; text-align:center; vertical-align:middle; padding:0; margin:0;">
    <div>
      Gear Motor
      <p style="margin-top:0;" align="left"><i>Figure 5.1: Gear Motor</i></p>
    </div>
    </td>
    <td>Operating voltage</td>
    <td>5–12V DC</td>
  </tr>
  <tr>
    <td>Rotation Speed</td>
    <td>450 RPM @ 12V</td>
  </tr>
  <tr>
    <td>Encoder Voltage</td>
    <td>3.3–5V DC</td>
  </tr>
  <tr>
    <td colspan="3">Cylindrical brushed DC gear motors, available in 5 variants (two 6V, three 12V) with wide gear ratios.</td>
  </tr>
  <tr>
    <td colspan="3">No-load Current: 200 mA, Rated Current: 300 mA, Stall Current: 800 mA</td>
  </tr>
</table>

This motor is very advantageous for us, because it also has a built in encoder sensor. We use this encoder sensor to move certain amount of distance. It comes especially handy when going a distance according to lidar decisions. For example:
- Let's say we need to move until robot's front distance is less than some amount (say `40 cm`).
- If we write a conditional and move until some lidar value is achieved we can overshoot. That is because of low lidar frequency (which is `~5-7 hz`, this means robot can move forwards without considering lidar for `~142-200 ms`).
- But if we use encoder values and let's say start with `70 cm` distance from the wall, we can command the robot to go `30 cm`. This conditional is not bound to frequency of any electronical component ans is upto `~15-20 hz`. Which means robot can miss only for `~50-66 ms` (which is less than half).

>[!IMPORTANT]
>Motors can operate above or below nominal voltage; high voltages
may reduce lifespan.

#### 3.4.2.2 Connections and Pin Configuration

<div>
  Motor Pinout
  <p style="margin-top:0;"><i>Figure 5.2: Gear Motor Pinout</i></p>
</div>

### 3.4.3 Servo Motor (TD8120MG):

#### 3.4.3.1 Description and Features

<table align="center" style="width:80%; border-collapse:collapse;">
  <tr>
    <th colspan="3">Servo Motor</th>
  </tr>
  <tr>
    <td rowspan="4" style="height:350px; text-align:center; vertical-align:middle; padding:0; margin:0;">
    <div>
      Gear Motor
      <p style="margin-top:0;" align="left"><i>Figure 6.1: Servo Motor</i></p>
    </div>
    </td>
    <td>Rotation Angle</td>
    <td>0°–180°</td>
  </tr>
  <tr>
    <td>Speed</td>
    <td>0.13 s / 60° @ 6.0V</td>
  </tr>
  <tr>
    <td>Torque</td>
    <td>20 kg·cm @ 6.0V, 23 kg·cm @ 7.4V</td>
  </tr>
  <tr>
    <td>Operating Voltage</td>
    <td>4.8–8.4V</td>
  </tr>
  <tr>
    <td colspan="3">Digital control system, metal gearbox</td>
  </tr>
</table>

We are using this digital servo for our steering (using an Ackermann controller). We previously used an analog servo but we switched because of some reasons:
- Digital servos have more frequency. They accept commands with smaller delays than analog servos.
- They turn faster and more on point. While an analog servo slowly reaches some steering point digital servos change their direction almost instantly.
- Has a greater precision. In comparison to analog servos we observed higher precision on turns, almost all turns made between countless tries were the same.

#### 3.4.3.2 Connections and Pin Configuration

<div>
  Servo Pinout
  <p style="margin-top:0;"><i>Figure 6.2: Servo Pinout</i></p>
</div>

### 3.5 LiDAR Sensor

#### 3.5.1 Definition and Model Features

Yahboom T-mini Plus LiDAR is a 2D lidar used for simple obstacle detection. Its main advantage is that it utilizes Time-of-Flight (ToF) measurement technology to deliver fast and accurate distance data. With high sampling frequency and good-enough
ambient light resistance, it performs well for our strategy.

<table align="center" style="width:80%; border-collapse:collapse;">
  <tr>
    <th colspan="3">Yahboom T-mini Plus LiDAR</th>
  </tr>
  <tr>
    <td rowspan="4" style="height:370px; text-align:center; vertical-align:middle; padding:0; margin:0;">
    <div>
      Gear Motor
      <p style="margin-top:0;" align="left"><i>Figure 7.1: Yahboom T-mini Plus LiDAR</i></p>
    </div>
    </td>
    <td>Measurement Range</td>
    <td>0.1 – 12 m (reflectivity-dependent)</td>
  </tr>
  <tr>
    <td>Scan Frequency</td>
    <td>1 – 10 Hz adjustable</td>
  </tr>
  <tr>
    <td>Sampling Rate</td>
    <td>up to 5000 samples/s</td>
  </tr>
  <tr>
    <td>Power requirements</td>
    <td>5V 300mA</td>
  </tr>
</table>

Lidar is used for scanning along the robot's Z-axis. It gives us output in (angle in radians, distance in meters) format. We convert it into (angle in degrees, distance in centimeters) format to make it easier for us to use the values and visualize it. In our robot lidar is used for: detecting the obstacles and finding the tilt of robot according to its surroundings. You can find more info about its usage in [Programming documentation](/src/).

## 3.6 Camera

We are using a camera for detecting colors. There is no other usage of camera in our robot, as we are detecting the obstacle without it (as mentioned before we are using the lidar).

### 3.6.1 Definition and Features

<table align="center" style="width:80%; border-collapse:collapse;">
  <tr>
    <th colspan="3">Camera Module 3</th>
  </tr>
  <tr>
    <td rowspan="3" style="height:370px; text-align:center; vertical-align:middle; padding:0; margin:0;">
    <div>
      Gear Motor
      <p style="margin-top:0;" align="left"><i>Figure 8.1: Camera Module </i></p>
    </div>
    </td>
    <td>Resolution</td>
    <td>11.9 MP (4608 × 2592)</td>
  </tr>
  <tr>
    <td>Pixel Size</td>
    <td>1.4 μm × 1.4 μm</td>
  </tr>
  <tr>
    <td>Video Modes</td>
    <td>1080p50 / 720p100 / 480p120</td>
  </tr>
  <tr>
    <td colspan="3">Connects via CSI-2 camera port</td>
  </tr>
  <tr>
    <td colspan="3">Power is supplied directly from the Raspberry Pi board via CSI-2
  interface</td>
  </tr>
</table>

The reason why we selected this camera is that it supports HDR mode, phase-detection autofocus (PDAF) for fast focusing. This is the main take-point for us, as the resolution of the camera is not really different between similar models. We already use it in `1586 x 864` mode for lower system usage and faster proccess time.

### 3.7 Gyroscope Sensor

#### 3.7.1 Definition and Features

<table align="center" style="width:80%; border-collapse:collapse;">
  <tr>
    <th colspan="3">BNO085</th>
  </tr>
  <tr>
    <td rowspan="2" style="height:370px; text-align:center; vertical-align:middle; padding:0; margin:0;">
    <div>
      Gear Motor
      <p style="margin-top:0;" align="left"><i>Figure 9.1: BNO085</i></p>
    </div>
    </td>
    <td>Orientation output</td>
    <td>Euler vector, up to 200 Hz</td>
  </tr>
  <tr>
    <td>Operating voltage</td>
    <td>3.3V typical 3.5mA</td>
  </tr>
</table>

Our gyro has a built-in fusion algorithm, which means it can in theory fuse accelerometer, magnotemeter and gyroscope. Despite all the advantages in theory, our IMU has a great drift over time. To fix this issue we implemented some algorithms and they are referenced in [Programming documentation](/src/).

### 3.8 Ultrasonic Sensor

#### 3.8.1 Definition and Features

<table align="center" style="width:80%; border-collapse:collapse;">
  <tr>
    <th colspan="3">HC-SR04</th>
  </tr>
  <tr>
    <td rowspan="4" style="height:370px; text-align:center; vertical-align:middle; padding:0; margin:0;">
    <div>
      Gear Motor
      <p style="margin-top:0;" align="left"><i>Figure 10.1: HC-SR04</i></p>
    </div>
    </td>
    <td>Operating Voltage & Current</td>
    <td>5V DC, 15 mA</td>
  </tr>
  <tr>
    <td>Ranging Distance</td>
    <td>2 cm to 400 cm</td>
  </tr>
  <tr>
    <td>Ranging Distance</td>
    <td>2 cm to 400 cm</td>
  </tr>
  <tr>
    <td>Accuracy</td>
    <td>~3mm</td>
  </tr>
  <tr>
    <td colspan="3">Measuring Angle,<15∘ cone;</td>
  </tr>
  <tr>
    <td colspan="3">A whopping frequency of 40kHz</td>
  </tr>
</table>

Altough this sensor support `2cm-400cm` range in theory, in reality with Raspberry Pi the best we could achive is a `10cm-70cm` range. Despite the difference this range is enough for us.

As we anticipated, the main technical challenge with our ultrasonic sensor is the voltage mismatch: the HC-SR04 sensor outputs its signal at 5 Volt (5V) logic, but the Raspberry Pi's GPIO pins are strictly limited to 3.3V. Connecting them directly would risk damaging the Pi's processor.

To solve this issue we developed a solution: By using specific resistors (i.e 1kΩ and 2kΩ) on the sensor's ECHO output line, we have successfully stepped down the voltage from 5V to a safe level of approximately 3.3V. This setup guarantees that the Raspberry Pi is protected from overvoltage damage while still receiving an accurate, readable digital signal.

To know which resistors should be used, we took advantage of level-shifting formula:

$$V_{\text{out}} = V_{\text{in}} \times \frac{R_2}{R_1 + R_2} \implies 5\text{V} \times \frac{2\text{k}\Omega}{1\text{k}\Omega + 2\text{k}\Omega} \approx 3.33\text{V}$$

<table align="center" cellspacing="0" cellpadding="0" style="margin:0; padding:0; border-collapse:collapse;">
  <tr>
    <th colspan="2">Level Shifting</th>
  </tr>
  <tr>
    <td align="center" style="margin:0; padding:0;"><br><i>Figure 10.2: Diagram to show how voltage is remapped</i></td>
    <td align="center"><br><i>Figure 10.3: To show the electric circuit</i></td>
  </tr>
</table>

**3.9. Custom PCB Design**

#### 3.9.1. Function and Purpose

To make our electronics more compact we decided to design a custom PCB. The PCB includes our LEDs, buzzer, button, switch and etc.

#### 3.9.2. Circuit Elements and Layer Structure

The circuit is built on a dual-layer PCB and includes the following key components:

- **Two LEDs (red and green):** Used as status and warning indicators.
- **Buzzer:** Provides audible alerts.
- **Push button:** User input control.
- **Fuse:** Overcurrent protection.
- **BNO085:** Orientation and motion sensing.
- **One switch:** Power on/off control.
- **Raspberry Pi 5 GPIO connections:** For system control and
  communication.
- **Ultraconic sensor:** For measure distance.
- **Capacitor:** For sudden surges.
- **One ferrit bead:** For EMI.

On the PCB, power lines are routed with thick copper wires, while signal lines are routed with thinner wires to ensure current handling capacity and minimize interference.

<table align="center" cellspacing="0" cellpadding="0" style="margin:0; padding:0; border-collapse:collapse;">
  <tr>
    <th colspan="2">Board 1</th>
  </tr>
  <tr>
    <td align="center" style="margin:0; padding:0;"><br><i>Figure 11.1: 3D view of first PCB board</i></td>
    <td align="center"><br><i>Figure 11.2: 2D view of first PCB board</i></td>
  </tr>
</table>

<table align="center" cellspacing="0" cellpadding="0" style="margin:0; padding:0; border-collapse:collapse;">
  <tr>
    <th colspan="2">Board 2</th>
  </tr>
  <tr>
    <td align="center" style="margin:0; padding:0;"><br><i>Figure 11.3: 3D view of second PCB board</i></td>
    <td align="center"><br><i>Figure 11.4: 2D view of second PCB board</i></td>
  </tr>
</table>

#### **3.9.3. Connection Points**

- **Power Input:** Operates with an external power supply of **6--14
  V**.
- **Raspberry Pi 5 GPIO:** Direct connections for LEDs, button, buzzer,
  and the sensor.
- **Sensor Connection:** The BNO085 IMU is connected via the **I²C
  interface (SCL, SDA)** to the Raspberry Pi 5.
- **Connectors:** JST and pin header connectors are used for both power
  and signal interfaces.

#### 3.9.4 Hardware Issues and Troubleshooting Process

At the beginning, we were using the **Hiwonder RRC Lite Controller**. At first glance, it appeared to be an ideal solution for our needs --- a single board that could easily interface with the Raspberry Pi, included a buzzer, button, encoder motor driver, and servo
ports, and seemed capable of handling all our system requirements.

However, as we started using it, we began experiencing connection
losses between the Raspberry Pi 5 and the controller while the
robot was operating. Initially, we didn't pay much attention to it since
the disconnections were quite rare. But over time, the issue worsened
--- what started as a once-a-week problem eventually became three to
four disconnections per day during testing.

We investigated the possible causes. Our first assumption was **EMI
(Electromagnetic Interference)** since the data cable was routed close
to the motor. To address this, we added a ferrite bead to the cable,
but it didn't help. Then we suspected a power issue, so we separated
the power connection and supplied the Raspberry Pi from an external
power bank instead. Unfortunately, the problem persisted.

We also added capacitors to the power input and replaced the cables,
yet the RRC Lite Controller continued to malfunction. Eventually, we
decided to design our own motor driver board to ensure stable
operation.

<table align="center" cellspacing="0" cellpadding="0" style="margin:0; padding:0; border-collapse:collapse;">
  <tr>
    <th colspan="2">Motor driver board</th>
  </tr>
  <tr>
    <td align="center" style="margin:0; padding:0;"><br><i>Figure 11.5: 3D view of our motor driver PCB board</i></td>
    <td align="center"><br><i>Figure 11.6: 2D view of our motor driver PCB board</i></td>
  </tr>
</table>

#### 3.9.5 PCB Layer Structure and Design Rules

- The PCB design was implemented on a **two-layer FR4 board**,
  manufactured by **JLCPCB**.
- The **top layer** carries most of the signal traces, while the
  **bottom layer** mainly serves as a **ground plane** to ensure stable
  reference potential and reduce noise.
- **Thicker copper traces** were used for power distribution lines,
  while **thinner traces** were used for signal routing.
- Design rules followed JLCPCB's recommended minimum clearance, trace
  width, and via size specifications.
- The layout was optimized to **minimize electromagnetic interference
  (EMI)** between the IMU sensor and the power circuits.
- A solid ground plane helps reduce sensor noise and improve overall
  system stability.

#### 3.9.6 Connectors and Component Placement

- **Connectors:** JST connectors and pin headers were used to allow easy
  connection of external modules such as the battery, button, and
  display.
- **Placement:**
  - The **Raspberry Pi 5 GPIO header** is positioned near the center for
    organized wiring and balanced routing.
  - **LEDs, buzzer, and button** are placed at the edge of the board for
    easy user access.
  - **Power input, fuse, and switch** are grouped together in a
    dedicated **power section**.
  - The **IMU sensor** is placed close to the GPIO pins to keep I²C
    lines short and reduce signal distortion.
- The two-layer layout also allows sensitive signal traces (such as I²C
  lines) to be routed over a continuous ground plane for improved noise
  shielding.

#### 3.9.7 Circuit Schemes

<table align="center" cellspacing="0" cellpadding="0" style="margin:0; padding:0; border-collapse:collapse;">
  <tr>
    <th colspan="1">Circuit Schemes</th>
  </tr>
  <tr>
    <td align="center" style="margin:0; padding:0;"><br><i>Figure 11.7: Control Board scheme</i></td>
  </tr>
  <tr>
    <td align="center"><br><i>Figure 11.8: Motor Driver scheme</i></td>
  </tr>
</table>

### 3.9.8 Manufacturing and Assembly Notes

- The PCB was fabricated by **JLCPCB** using **FR4 material (1.6 mm
  thickness, 1 oz copper)** with **green solder mask** and **white
  silkscreen**.
- The inclusion of **solder mask** and **silkscreen layers** simplified
  soldering and improved assembly accuracy.
- Assembly was performed manually, using **through-hole (THT)**
  components and a few **surface-mount (SMD)** parts.
- **Thicker traces** were used for power paths, while **narrower ones**
  were used for signal lines.
- Compared to the initial perfboard prototype, the final 2-layer PCB
  offers **greater durability, improved signal integrity, and a more
  professional appearance**.

**3.9.9 GERBER Files**

>[!NOTE]
> If you want to order PCB(Printed Circuit Board), download these `GERBER` files and follow the steps in the video.

<table align="center" cellspacing="0" cellpadding="0" style="margin:0; padding:0; border-collapse:collapse;">
  <tr>
    <th colspan="4">PCB Files</th>
  </tr>
  <tr>
    <th>Name</th>
    <th>GERBER</th>
    <th>BOM</th>
    <th>Pick & Place</th>
  </tr>
  <tr>
    <td>Raspberry Pi Distributon Board 1</td>
    <td><a href="dist1.zip">dist1.zip</a></td>
    <td><a href="bom1.xlsx">bom1.xlsx</a></td>
    <td><a href="pnp1.xlsx">pnp1.xlsx</a></td>
  </tr>
  <tr>
    <td>Raspberry Pi Distributon Board 2</td>
    <td><a href="dist2.zip">dist1.zip</a></td>
    <td><a href="bom2.xlsx">bom1.xlsx</a></td>
    <td><a href="pnp2.xlsx">pnp1.xlsx</a></td>
  </tr>
  <tr>
    <td>Motor Driver</td>
    <td><a href="dist3.zip">dist1.zip</a></td>
    <td><a href="bom3.xlsx">bom1.xlsx</a></td>
    <td><a href="pnp3.xlsx">pnp1.xlsx</a></td>
  </tr>
</table>

> [!NOTE]
> If you don\'t know how to order a PCB, click the link and watch this [video](https://www.youtube.com/watch?v=SGsfiHOE9Fk&t=466s).

## 3.10 Power Supply (3S Li-Po Battery)

### 3.10.1 Battery Specifications (Voltage, Capacity, C Rating)

The power source of the project is a **JetFire 3S Li-Po battery**,
specifically designed for high-current demanding applications such as
robotics, drones, and defense systems. Thanks to its high discharge rate
and reliable cell quality, it ensures stable and long-term operation.

Technical Specifications:
- Voltage: **11.1 V** (nominal)
- Capacity: **1300 mAh**
- Cells: **3S (3 cells in series)**
- Discharge Rate: **50C continuous / 100C peak (max 10s)**
- Weight: **110 g**
- Dimensions: **74 × 33 × 21 mm**
- Discharge Connector: **XT60 (black)**
- Charging Connector: **JST-XHR (white)**

### 3.10.2 Power Management Circuits (BMS, Charging Circuit)

Li-Po batteries require safe charging and monitoring systems. A
**Battery Management System (BMS)** or balance charger must be used to:
- Monitor individual cell voltages,
- Prevent overcharging or deep discharge,
- Provide safe current limits during operation.
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

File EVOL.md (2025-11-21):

<table align="center" cellspacing="0" cellpadding="0" style="margin:0; padding:0; border-collapse:collapse;">
  <tr>
    <th colspan="3">Evolution Table</th>
  </tr>
  <tr>
    <td><h3><b>Specifications</b></h3></td>
    <td align="center" style="margin:0; padding:0;"></td>
    <td align="center"></td>
  </tr>
  <tr>
    <td>Controller</td>
    <td>Raspberry Pi 5, 8 GB RAM</td>
    <td>Raspberry Pi 5, 8 GB RAM</td>
  </tr>
    <tr>
    <td>Camera</td>
    <td>Raspberry Pi Camera Module 3</td>
    <td>Raspberry Pi Camera Module 3</td>
  </tr>
    <tr>
    <td>Lidar</td>
    <td>RPLidar A1M8</td>
    <td>Yahboom T-MINI-PLUS</td>
  </tr>
    <tr>
    <td>IMU</td>
    <td>BNO055</td>
    <td>BNO085</td>
  </tr>
    <tr>
    <td>Servo Motor</td>
    <td>MG995 (Analog)</td>
    <td>TD8120MG (Digital)</td>
  </tr>
    <tr>
    <td>Boards</td>
    <td>Prefboard</td>
    <td>PCB</td>
  </tr>
    <tr>
    <td>Ackermann Geometry</td>
    <td>Not exactly (some minor issues)</td>
    <td>Yes (fixed those issues)</td>
  </tr>
    <tr>
    <td>Motor Driver</td>
    <td>DRV8833</td>
    <td>TB6612FNG</td>
  </tr>
    <tr>
    <td>Motor Drive Controller</td>
    <td>Raspberry Pi Pico 2</td>
    <td>Raspberry Pi Pico W</td>
  </tr>
</table>

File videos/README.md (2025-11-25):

<table align="center" cellspacing="0" cellpadding="0" style="margin:0; padding:0; border-collapse:collapse;">
  <tr>
    <th colspan="2">Videos</th>
  </tr>
  <tr>
    <td align="center">
        <a href="https://www.youtube.com/watch?v=vvl1z-_QSYw&list=PLiso-udvas0ohQMEMukKzdqdF-Q77ta-R">
        <br>
        </a>
      <b>Open Challenge</b>
    </td>
    <td align="center">
        <a href="https://www.youtube.com/watch?v=AqHtKbuUQjM&list=PLiso-udvas0ohQMEMukKzdqdF-Q77ta-R&index=4">
        <br>
        </a>
      <b>Open Challenge Commentary</b>
    </td>
  </tr>
  <tr>
    <td align="center">
        <a href="https://www.youtube.com/watch?v=panU9ucA8hE&list=PLiso-udvas0ohQMEMukKzdqdF-Q77ta-R&index=1">
        <br>
        </a>
      <b>Obstacle Challenge</b>
    </td>
    <td align="center">
        <a href="https://www.youtube.com/watch?v=kVnSEkZt-Fs&list=PLiso-udvas0ohQMEMukKzdqdF-Q77ta-R&index=3">
        <br>
        </a>
      <b>Obstacle Challenge Documentation</b>
    </td>
  </tr>
</table>

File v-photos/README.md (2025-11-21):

<table align="center" cellspacing="0" cellpadding="0" style="margin:0; padding:0; border-collapse:collapse;">
  <tr>
    <th colspan="4">Robot Photos</th>
  </tr>
  <tr>
    <td align="center" colspan="2">
      <br>
      <b>Right</b>
    </td>
    <td align="center" colspan="2">
      <br>
      <b>Left</b>
    </td>
  </tr>
  <tr>
    <td align="center">
      <br>
      <b>Top</b>
    </td>
    <td align="center">
      <br>
      <b>Front</b>
    </td>
    <td align="center">
      <br>
      <b>Back</b>
    </td>
    <td align="center">
      <br>
      <b>Bottom</b>
    </td>
  </tr>
</table>

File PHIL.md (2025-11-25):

In our working environment we had a whiteboard. We used this whiteboard to note everything we have done, our break times, what we are going to do, and how much time is left before the competition. We also had some notes to support us physchologically. We recently found a picture of our whiteboard from nationaly qualifications. It had these notes that we wanted to share as our philosophy and habits:

- Don't be pessimist (We have written this, because we were having some bad time with our motor driver and it influenced our mental a little bit).
- Don't mind other stuff than the competition when inside the room (We were having some conversations about other stuff at the beginning of our preperations, then we realized it is just waste of our precious time for competition).
- Always plan what you are going to do before coming to the room (We sometimes just went to the working lab and did not know what to do, it took us extra time to think what to do today. To prevent this time waste we added this rule).
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

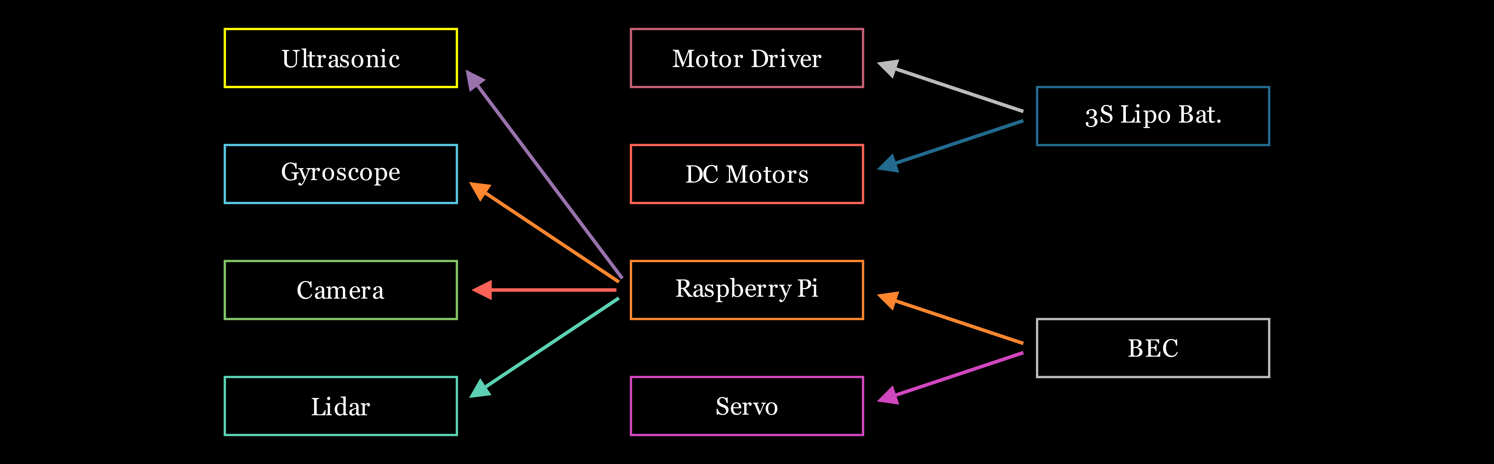
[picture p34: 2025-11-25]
media/electronics_block.png

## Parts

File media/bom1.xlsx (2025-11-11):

Comment | Designator | Footprint | Pin Count | Layer | Mounting Style | 3D Model Transform | Unique ID | Device | Name | 3D Model Title
JST-XHP-2-PIN | LIGHTS1 | JST-XHP-2-PIN | 2 | T | DIP | 291.34,227.265,0,0,0,0,0.001,-20.67,-131.89 | gge88507 | JST-XHP-2-PIN | JST-XHP-2-PIN | JST_XH2.54_2P
1k | R10,R11,R12 | R0805 | 2 | T | SMT | 78.74,51.181,0,0,0,0,-0.001,-0.001,0 | gge5c9e7bad51cc1325,ggea31eb37460e6e215,ggef05cc37f92fb6a35 | 1k | 1k | R0805_L2.0-W1.3-H0.6
0603 CAPACITOR | REF1 | 0603 CAPACITOR | 2 | T | SMT | 63.056,39.37,0,0,0,0,0,0.001,0 | gge253208 | 0603 CAPACITOR | 0603 CAPACITOR | 0805 Capacitor
0805 CAPACITOR | U1,U18 | 0805 CAPACITOR | 2 | T | SMT | 94.584,59.055,0,0,0,0,-0.434,0.001,0 | gge26e0cc38ddb90ff1,gge253415 | 0805 CAPACITOR | 0805 CAPACITOR | 0805 Capacitor
JST-XH-2.54-8P | U2 | JST-XH-2.54-8P | 8 | T | DIP | 885.825,228.346,0,180,0,0,351.927,-20.669,-125.984 | gge276244 | JST-XH-2.54-8P | JST-XH-2.54-8P | CONN-TH_8P-P2.50-XH2.54-8P
ADAFRUIT-BNO085-NO-PADS | U3 | ADAFRUIT-BNO085-NO-PADS | 0 | T | SMT | 1000,900,0,0,0,0,257.047,352.913,39.37 | gge176623 | ADAFRUIT-BNO085-NO-PADS | ADAFRUIT-BNO085-NO-PADS | Adafruit BNO085 STEMMA QT
DO-214AA_L4.4-W3.6-LS5.3-RD | U5 | DO-214AA_L4.4-W3.6-LS5.3-RD | 2 | T | SMT | 209.8421,141.732,0,0,0,0,0,-0.001,0 | gge257937 | DO-214AA_L4.4-W3.6-LS5.3-RD | DO-214AA_L4.4-W3.6-LS5.3-RD | DO-214AA_L4.4-W3.6-LS5.3-RD
LED 3MM GREEN TH | U6,U15 | LED 3MM GREEN TH | 2 | T | DIP | 142.52,154.826,0,0,0,0,-5.907,0,-137.795 | gge85054,ggee18805724e808788 | LED 3MM GREEN TH | LED 3MM GREEN TH | LED-TH-3mm_G

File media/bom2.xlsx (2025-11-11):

Comment | Designator | Footprint | Pin Count | Layer | Mounting Style | 3D Model Transform | Unique ID | Device | Name | 3D Model Title
JST-XHP-2-PIN | BUTTON,MONITOR,SWITCH | JST-XHP-2-PIN | 2 | T | DIP | 291.34,227.265,0,0,0,0,0,-20.669,-131.89 | gge140a593398eba8a7,gge01959b4423432824,gge88507 | JST-XHP-2-PIN | JST-XHP-2-PIN | JST_XH2.54_2P
KLEMENS | INPUT,OUTPUT | KLEMENS | 2 | T | DIP | 440.94396,421.259,0,90,0,0,23.425,96.26,-196.85 | gge106126,gge106198 | KLEMENS | KLEMENS | CONN-TH_2P-P5.00_WJ129V-5.00-2P
40PIN | J1 | 40PIN | 40 | T | DIP | 2299.9954,348.41478,0,0,0,0,-0.511,0.511,-137.795 | gge73711 | 40PIN | 40PIN | HDR-IDC-2.54-2X40P
1k | R9,R12,R13 | R0805 | 2 | T | SMT | 78.74,51.181,0,0,0,0,0,0,0 | gge0c3b056fe453dd84,gge385efd279b6f3d15,gge1326baf3de469d4d | 1k | 1k | R0805_L2.0-W1.3-H0.6
0603 CAPACITOR | REF2 | 0603 CAPACITOR | 2 | T | SMT | 63.056,39.37,0,0,0,0,0,0,0 | gge7f723698900b5dd4 | 0603 CAPACITOR | 0603 CAPACITOR | 0805 Capacitor
JST-XH-2.54-8P | U2 | JST-XH-2.54-8P | 8 | T | DIP | 885.825,228.346,0,180,0,0,351.927,-20.669,-125.984 | gge276244 | JST-XH-2.54-8P | JST-XH-2.54-8P | CONN-TH_8P-P2.50-XH2.54-8P
BUZZER | U8 | BUZZER | 2 | T | DIP | 669.29,669.29,0,0,0,0,3.856,-3.386,-125.984 | gge89998 | BUZZER | BUZZER | BUZ-TH_BD22.0-P10.00_BUZZER_PIEZO_HX-2212
FUSE-HOLDER-WITH-COVER-FOR-5X20MM-FUSE_FOOTPRINT | U10 | FUSE-HOLDER-WITH-COVER-FOR-5X20MM-FUSE_FOOTPRINT | 2 | T | DIP | 984.25,385.307,0,0,0,0,0,0,-118.11 | gge95350 | FUSE-HOLDER-WITH-COVER-FOR-5X20MM-FUSE_FOOTPRINT | FUSE-HOLDER-WITH-COVER-FOR-5X20MM-FUSE_FOOTPRINT | FUSE-TH_L25.8-W10.5-P22.00
0805 CAPACITOR | U19 | 0805 CAPACITOR | 2 | T | SMT | 94.584,59.055,0,0,0,0,-0.435,0,0 | gge4a6c2c15f2022731 | 0805 CAPACITOR | 0805 CAPACITOR | 0805 Capacitor
JST-XHP-4-PIN | ULTRASONIC | JST-XHP-4-PIN | 4 | T | DIP | 488.19,409.451,0,180,270,0,0,-133.857,39.37 | gge91696 | JST-XHP-4-PIN | JST-XHP-4-PIN | Jst

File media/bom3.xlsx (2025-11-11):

Comment | Designator | Footprint | Pin Count | Layer | Mounting Style | 3D Model Transform | Unique ID | Device | Name | 3D Model Title
CAP470UF/25V | C1,C2 | CAP470UF/25V | 2 | T | DIP | 248.4247,247.99777,0,180,0,180,0,0,440.945 | gge293285,ggeb8e2660de8253b91 | CAP470UF/25V | CAP470UF/25V | CAP-TH_D6.3×H11.2×P2.5
JST-XH-6PIN-2.5 | J4 | JST-XH-6PIN-2.5 | 6 | T | DIP | 669.29,226.96,0,0,0,0,-0.001,19.686,-114.173 | gge5f7d5e20379302eb | JST-XH-6PIN-2.5 | JST-XH-6PIN-2.5 | jst-xh-6p
TB6612FNG | M1 | TB6612FNG | 16 | T | DIP | 480,834.431,0,0,0,270,717.61,-334.427,0 | gge150610 | TB6612FNG | TB6612FNG | TB6612FNG MODULO
PINHEADER1X8N-3D-C | P1 | PINHEADER1X8N-3D-C | 8 | T | DIP | 100,799.998,0,90,0,0,149.604,0,-118.11 | gge291123 | PINHEADER1X8N-3D-C | PINHEADER1X8N-3D-C | PinHeader_1x08_P2.54mm_Vertical
1k | R10 | R0805 | 2 | T | SMT | 78.74,51.181,0,0,0,0,0,0,0 | ggef05cc37f92fb6a35 | 1k | 1k | R0805_L2.0-W1.3-H0.6
0603 CAPACITOR | REF1,REF2,REF3 | 0603 CAPACITOR | 2 | T | SMT | 63.056,39.37,0,0,0,0,0,0,0 | gge0eeba559b048769e,gge253208,ggecebe1e1831d76673 | 0603 CAPACITOR | 0603 CAPACITOR | 0805 Capacitor
0805 CAPACITOR | U1,U22,U23 | 0805 CAPACITOR | 2 | T | SMT | 94.584,59.055,0,0,0,0,-0.435,0,0 | gge9360ead03746660b,gge253415,ggec6adf27a0aa830e9 | 0805 CAPACITOR | 0805 CAPACITOR | 0805 Capacitor
JST-XHP-3-PIN | U2 | JST-XHP-3-PIN | 3 | T | DIP | 389.76,222.083,0,180,0,0,-1.576,-20.67,-125.984 | gge264179 | JST-XHP-3-PIN | JST-XHP-3-PIN | JST-3pin
TERMINAL BLOCK CY350-3.5 2PIN 3.5MM PITCH 300V 10A | U4,U20,U21 | TERMINAL BLOCK CY350-3.5 2PIN 3.5MM PITCH 300V 10A | 2 | T | DIP | 313.39,478.288,0,0,90,0,-0.001,137.795,98.425 | gge9bed89732678624f,gge284978,ggec0cf4850c577dbe9 | TERMINAL BLOCK CY350-3.5 2PIN 3.5MM PITCH 300V 10A | TERMINAL BLOCK CY350-3.5 2PIN 3.5MM PITCH 300V 10A | 2445p-screw-terminal-block-2-pin-3-5mm-pitch-side-entry-1.snapshot.1/2445P Screw Terminal Block- 2 Pin, 3.5mm Pitch, Side Entry/2445p screw terminal block- 2 pin, 3.5mm pitch, side entry
LED 3MM GREEN TH | U15 | LED 3MM GREEN TH | 2 | T | DIP | 142.52,154.826,0,0,0,0,-5.906,-0.001,-137.795 | ggee18805724e808788 | LED 3MM GREEN TH | LED 3MM GREEN TH | LED-TH-3mm_G
RASPBERRY PI PICO/ RASPBERRY PI PICO W | U17 | RASPBERRY PI PICO/ RASPBERRY PI PICO W | 40 | T | DIP | 826.77,2063.32,0,0,0,0,413.385,1029.525,0 | gge242796 | RASPBERRY PI PICO/ RASPBERRY PI PICO W | RASPBERRY PI PICO/ RASPBERRY PI PICO W | raspberrypi pico w.step

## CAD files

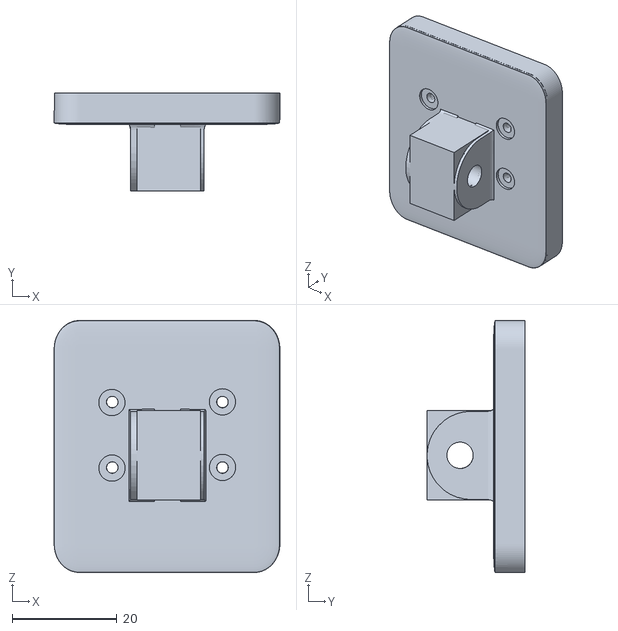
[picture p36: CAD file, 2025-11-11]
models/camera_holder.stl
43.0 x 18.7 x 48.0

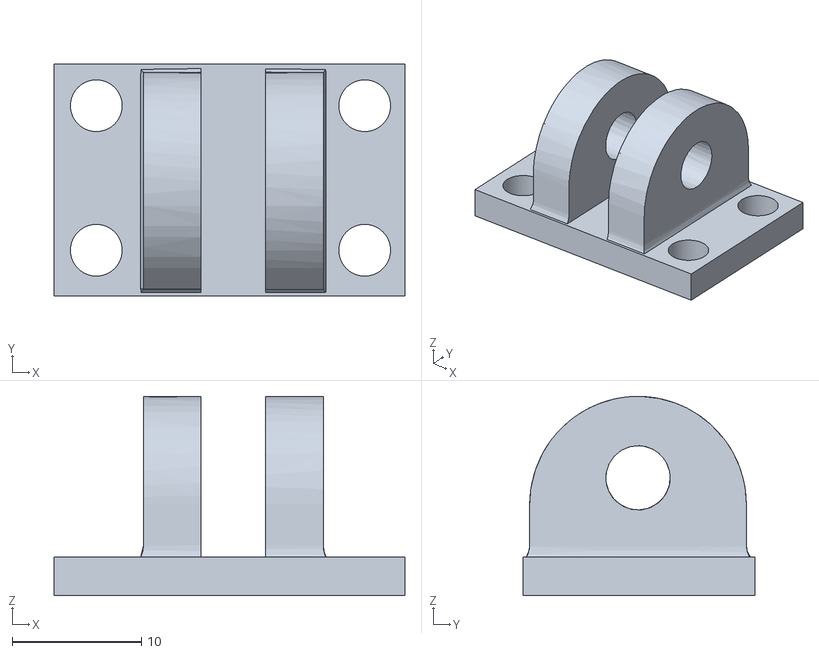
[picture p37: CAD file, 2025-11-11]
models/camera_steering_holder.stl
27.2 x 18.0 x 15.4

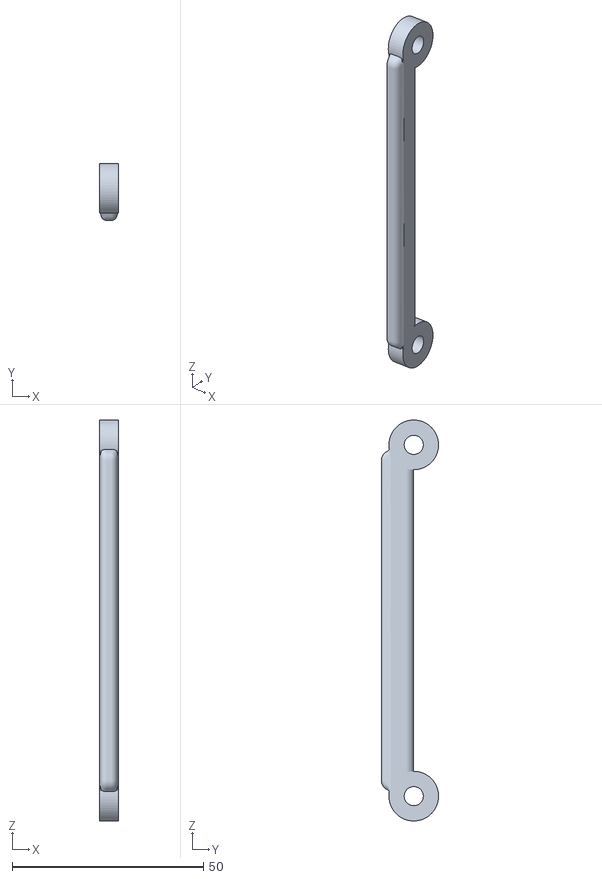
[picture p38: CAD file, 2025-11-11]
models/camera_steering.stl
4.91 x 15.0 x 104.8

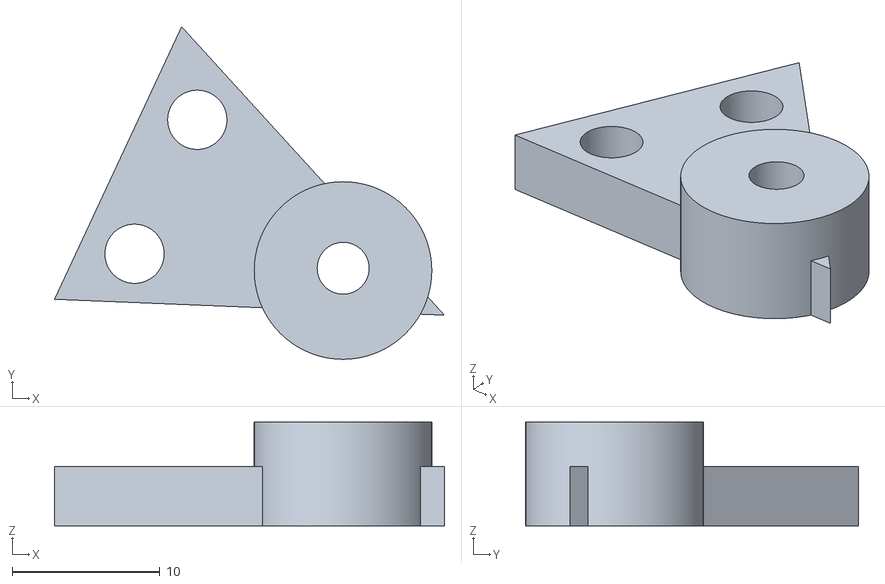
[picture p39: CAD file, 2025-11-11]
models/front_wheel_holder.stl
26.4 x 22.5 x 7.00

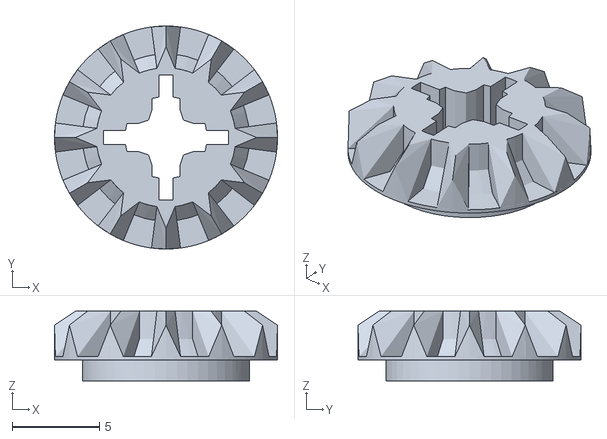
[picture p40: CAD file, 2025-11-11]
models/gear_box_wheel.stl
12.8 x 12.8 x 4.00

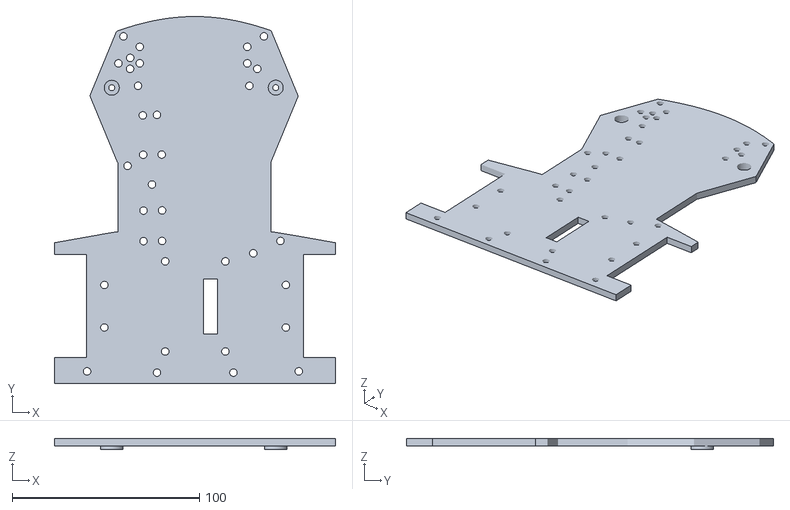
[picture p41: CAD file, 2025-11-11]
models/car_chassis_down_part.stl
150.0 x 195.9 x 6.00

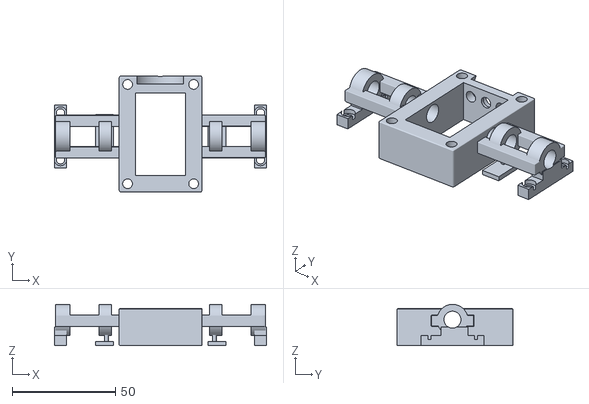
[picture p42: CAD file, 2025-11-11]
models/motor_box.stl
102.7 x 56.1 x 20.0

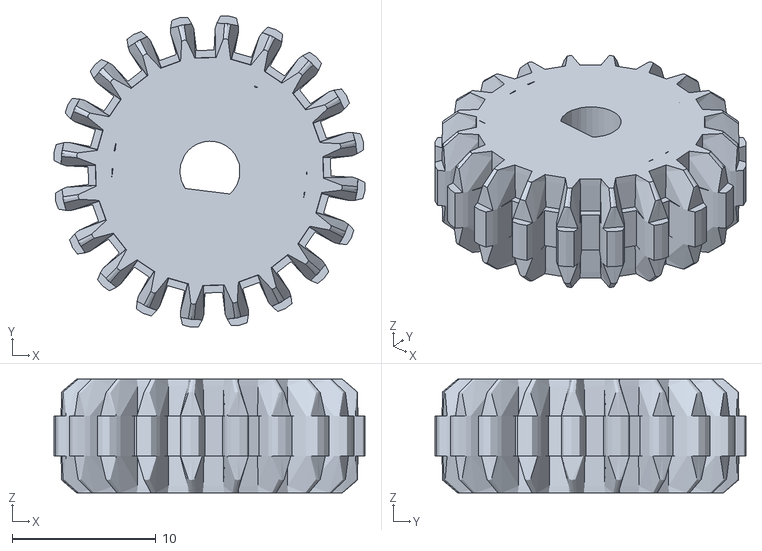
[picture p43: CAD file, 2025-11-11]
models/motor_box_wheel.stl
21.6 x 21.6 x 7.92

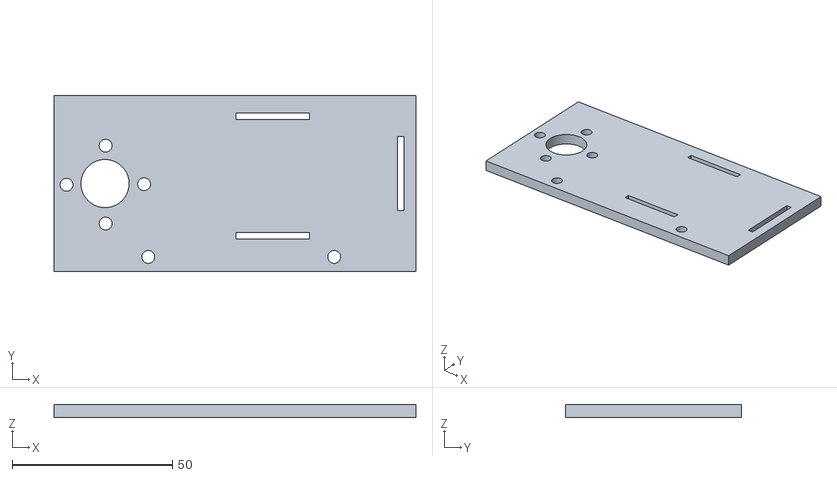
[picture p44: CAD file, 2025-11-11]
models/battery_holder.stl
112.9 x 55.0 x 4.00

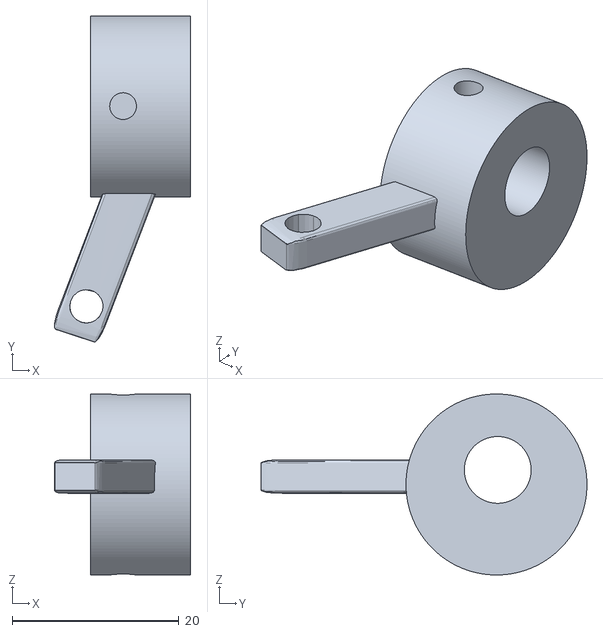
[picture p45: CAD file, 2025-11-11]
models/wheel_steering_system_left.stl
16.3 x 39.1 x 21.7

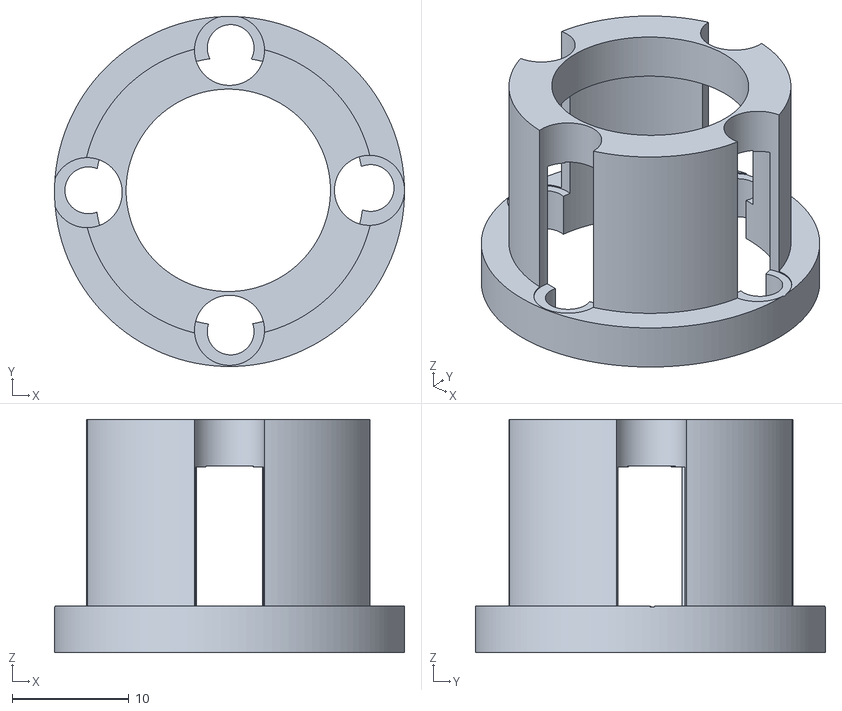
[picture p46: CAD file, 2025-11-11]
models/button_holder.stl
30.0 x 30.0 x 20.0

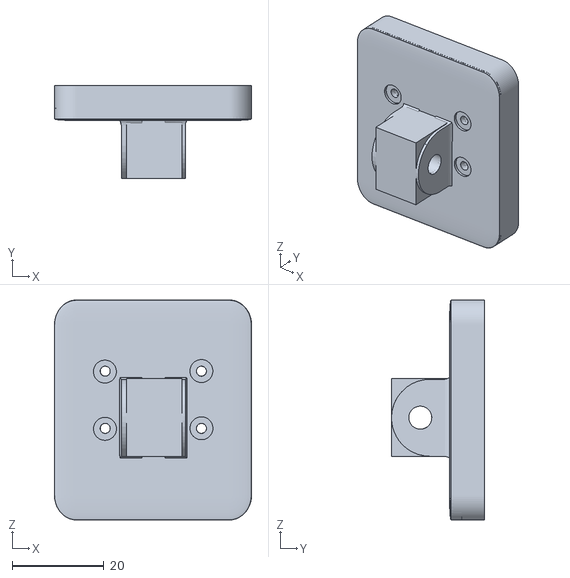
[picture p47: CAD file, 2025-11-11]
models/camera_holder_2.stl
43.0 x 20.3 x 48.0

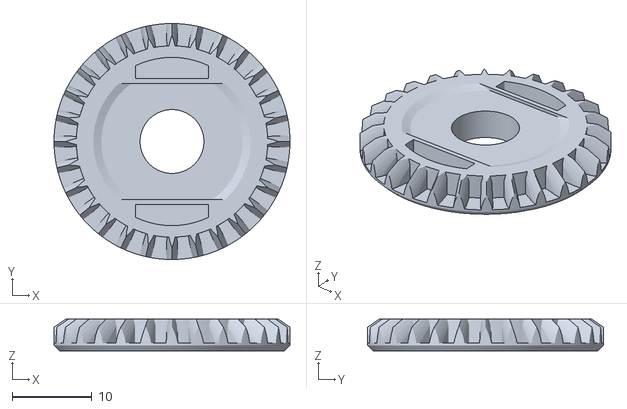
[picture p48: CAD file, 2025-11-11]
models/motor_box_wheel_ 62821.stl
29.6 x 29.6 x 4.00

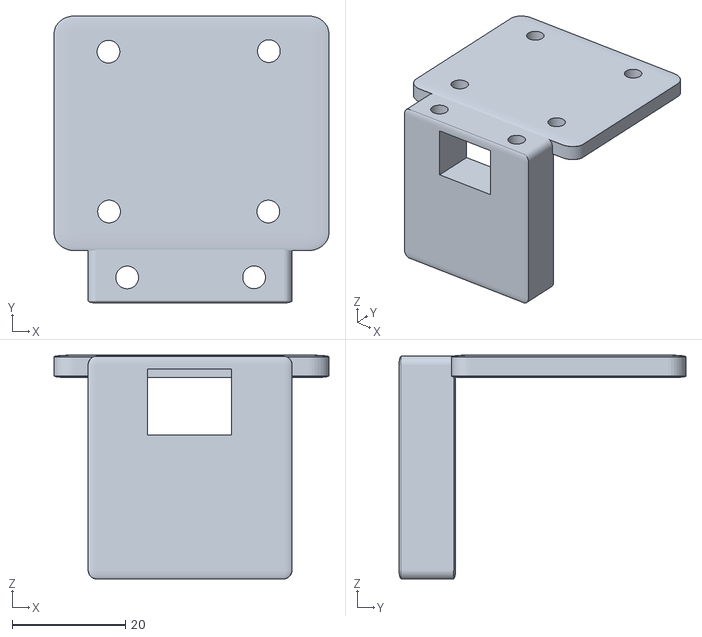
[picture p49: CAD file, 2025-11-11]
models/lidar_holder.stl
48.5 x 50.6 x 39.5

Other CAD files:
models/wheel_steering_system_right.stl
models/ultrasonic_holder.stl
models/servo_motor_bracket.stl
models/motor_box_wheel_ 62821_2.stl
models/car_chassis_upper_part.stl

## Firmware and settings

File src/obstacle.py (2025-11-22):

import cv2
import math
import time
import numpy
import gpiozero
import robot_car
import rclpy.node
import sensor_msgs.msg

from rclpy.qos import QoSProfile, QoSReliabilityPolicy

LEFT_BACK = (31.2637317, 16.3783393542)
ROBOT_LENGTH = 22

START = 0
KUBIK_UC = 1
KUBIK_TC = 2
BASE_WALL = 3
FOR_WALL = 4
NARROW = 5
SKEW = 6
SCREW_RIGHT = 7
PUT_BAGS = 8
ADJUST_DIS = 9
FIN_1 = 10
FIN_2 = 11
FIX_GYRO_1 = 12
FIX_GYRO_2 = 13

SKEW_RED = 14
GO_BACK_RED = 15
PUT_BAGS_RED = 16
ADJUST_DIS_RED = 17
SCREW_LEFT_RED = 18

GREEN = 0
RED = 1

class miav(rclpy.node.Node):
    def __init__(self):
        super().__init__('miav')
        qos = QoSProfile(depth=10,reliability=QoSReliabilityPolicy.BEST_EFFORT)
        self.create_subscription(sensor_msgs.msg.LaserScan, '/scan', self.scan_callback, qos)
        self.create_subscription(sensor_msgs.msg.CompressedImage, '/camera/image_raw/compressed', self.camera_callback, 1)
        self.create_timer(1 / 20, self.miav_callback)

        self.dir = None
        self.f_dir = False

        self.off_x = 35
        self.off_y = 15

        self.color = None
        self.colors = {
            'green': [((70, 128, 75), (86, 255, 170)), ((67, 106, 22), (78, 188, 182)), ((69, 51, 33), (95, 193, 154)), ((59, 93, 58), (79, 229, 147)), ((18, 27, 88), (97, 188, 156))],
            'red': [((0, 154, 160), (179, 206, 235)), ((0, 113, 0), (8, 255, 255)), ((0, 40, 124), (1, 219, 196)), ((170, 76, 159), (180, 255, 215))],
        }

        self.e = None

        self.kubik = None
        self.turned = False
        self.narrow = False
        self.wall_dis = None
        self.kubik_pos = None
        self.swing_ang = None
        self.start_pos = None
        self.skew_done = False
        self.manoeuvre = False
        self.color_val = False
        self.target_dis = None
        self.gone_back = False
        self.get_close = False
        self.face_kubik = False
        self.last_back_dis = None

        self.exec = START
        self.waitin = None
        self.time = None

        self.idle = False
        self.idle_speed = None

        robot_car.read_encoder()

        self.kubiks = []
        self.kubik_ix = -1
        self.last_kubik = None
        self.last_dis = None
        self.last_side = None
        self.last_ok = False
        self.on_this_side = 0
        self.seen_start = False
        self.lap_cnt = 0

        self.start_time = None

        self.count = 0

        self.park_mode = False

        self.mov_park = 0
        self.initial = None
        self.dis_till = None
        self.entr_ang = None
        self.back_dis = None
        self.left_dis = None
        self.right_dis = None
        self.front_dis = None

        self.last_color = RED
        self.d = True

        self.pt_one = None
        self.pt_two = None

    def find_katets(self, point):
        deg, hyp = point
        beta = math.radians(deg)
        adj = math.cos(beta) * hyp
        opp = math.sin(beta) * hyp
        return adj, opp

    def find_park(self, scan):
        ly1, ly2, lx1, lx2 = None, None, None, None
        for p in scan:
            var = (self.dir == 90 and (p[0] < -90 or p[0] > 30))
            if var:
                continue
            y_dis = abs(p[1] * math.sin(math.radians(90 + p[0])))
            x_dis = abs(p[1] * math.cos(math.radians(90 + p[0])))
            if y_dis > 100: return None
            if ly1 is None or abs(y_dis - ly1) > 3:
                if lx2 is not None and abs(lx2 - lx1) > 3:
                    return (lx2, ly1)
                ly1, ly2, lx1, lx2 = y_dis, y_dis, x_dis, x_dis
            else:
                ly2, lx2 = y_dis, x_dis
        return None

    def find_kubik(self, data, wall_dis):
        if wall_dis is None:
            return None

        left_lim = self.off_x - wall_dis
        right_lim = 100 - self.off_x - wall_dis

        if self.dir == -90:
            left_lim, right_lim = -right_lim, -left_lim

        closest, furthest = None, None

        for point in data:
            y_dis, x_dis = self.find_katets(point)
            if left_lim <= x_dis <= right_lim:
                if y_dis > self.off_y and (closest is None or closest[0] > y_dis):
                    closest = (y_dis, x_dis)
                if y_dis > self.off_y and (furthest is None or furthest[0] < y_dis):
                    furthest = (y_dis, x_dis)

        var = closest is not None and ((self.dir == 90 and closest[0] >= 95) or (self.dir == -90 and closest[0] >= 120))

        if closest is None or furthest is None or \
                furthest[0] - closest[0] <= 60 or \
                closest[0] <= 15 or var:
            return None

        if self.dir == 90:
            from_wall_dis = wall_dis + closest[1]
        elif self.dir == -90:
            from_wall_dis = wall_dis - closest[1]

        if (self.dir == 90 and from_wall_dis <= 50) or (self.dir == -90 and from_wall_dis <= 43):
            return 40, closest[0]
        else:
            return 60, closest[0]

    def find_wall(self, scan):
        wall = None
        for point in scan:
            y_dis, x_dis = self.find_katets(point)
            var = (self.dir == 90 and x_dis < 0) or (self.dir == -90 and x_dis > 0)
            if y_dis <= 10:
                var = wall is None or ((self.dir == 90 and x_dis < wall) or (self.dir == -90 and x_dis > wall))
                if var:
                    wall = x_dis
        if wall is not None:
            return abs(wall)
        return None

    def find_angle(self, a, b):
        (y1, x1), (y2, x2) = a, b
        dx, dy = abs(x2 - x1), abs(y2 - y1)
        return math.degrees(math.atan2(dy, dx))

    def scan_callback(self, msg):
        gyro_angle = robot_car.read_gyro()
        all_scan, scan, rad = [], [], msg.angle_min
        for dis in msg.ranges:
            deg = math.degrees(rad) + 90
            if deg >= 180: deg -= 360
            act_deg = gyro_angle + deg
            dis *= 100
            if dis != 0 and math.isfinite(dis) and -130 <= act_deg <= 130 and dis >= 13:
                scan.append((act_deg, dis))
            if dis != 0 and math.isfinite(dis) and -130 <= deg <= 130 and dis >= 13:
                all_scan.append((deg, dis))
            rad += msg.angle_increment
        scan.sort()
        all_scan.sort()

        self.al_left_dis = robot_car.find(min, all_scan, -95, -85)
        self.al_right_dis = robot_car.find(min, all_scan, 85, 95)

        self.left_dis = robot_car.find(min, scan, -92.5, -87.5)
        self.right_dis = robot_car.find(min, scan, 87.5, 92.5)
        self.front_dis = robot_car.find(min, scan, -2.5, 2.5)

        if self.waitin is not None:
            self.exec = self.waitin
            self.waitin = None
            return

        if self.park_mode:
            if self.exec is not None:
                return
            if self.last_color == GREEN:
                if self.mov_park < 1:
                    if self.dis_till is None:
                        park = self.find_park(scan)
                        self.dis_till = park
                        print('[DIS TILL]', park)
                    if self.dis_till is not None:
                        if self.start_pos is None and robot_car.pos is not None:
                            self.start_pos = robot_car.pos
                        if robot_car.pos is None or robot_car.rot_to_cm(robot_car.pos - self.start_pos) < self.dis_till[1] + \
                                (31, 1)[self.mov_park]:
                            err = -robot_car.read_gyro()
                            print('here?', robot_car.rot_to_cm(robot_car.pos - self.start_pos))
                            robot_car.move(err * 5, 30)
                        else:
                            self.mov_park += 1
                            self.dis_till = None
                            self.start_pos = None
                            robot_car.hard_brake()
                else:
                    self.exec = PUT_BAGS
            elif self.last_color == RED:
                dis_arr = (10, 25)
                if self.mov_park < 2:
                    if self.dis_till is None:
                        park = self.find_park(scan if self.dir == 90 else scan[::-1])
                        self.dis_till = park
                        if self.dis_till is None:
                            return
                        print('[DIS TILL]', park)
                    if self.dis_till is not None:
                        if self.start_pos is None and robot_car.pos is not None:
                            self.start_pos = robot_car.pos
                        if robot_car.pos is None or robot_car.rot_to_cm(robot_car.pos - self.start_pos) < self.dis_till[1] + \
                                dis_arr[self.mov_park]:
                            err = -robot_car.read_gyro()
                            print('here?', robot_car.rot_to_cm(robot_car.pos - self.start_pos))
                            robot_car.move(err * 5, 30)
                        else:
                            self.mov_park += 1
                            self.dis_till = None
                            self.start_pos = None
                            robot_car.hard_brake()
                            if self.dir == -90 and self.mov_park == 1 and not self.d:
                                self.exec = SKEW
                else:
                    if self.dir == 90:
                        self.exec = PUT_BAGS_RED
                    elif self.dir == -90:
                        self.exec = PUT_BAGS
            return

        if not self.f_dir:
            for_dis = robot_car.find(min, scan, -5, 5)
            left = robot_car.find(max, scan, -90, -10)
            right = robot_car.find(max, scan, 10, 90)
            if left is not None and (right is None or left > right):
                self.dir = -90
            else:
                self.dir = 90
            self.f_dir = True

        r_wall_dis = self.find_wall(scan)

        for_dis = robot_car.find(min, scan, -20, 20)

        self.wall_dis = r_wall_dis

        if self.dir == 90:
            self.side_dis = robot_car.find(min, scan, 85, 90)
        elif self.dir == -90:
            self.side_dis = robot_car.find(min, scan, -90, -85)
        
        self.for_dis = for_dis

        if self.exec is not None:
            return

        kubik = self.find_kubik(scan, r_wall_dis)

        if kubik is not None and self.on_this_side < 2:
            if self.count == 0:
                self.seen_start = True
            self.time = None
            self.kubik = kubik
            if self.count < 5:
                print('KUBIK FOUND', kubik)
                robot_car.move(0,101)
                self.exec = KUBIK_UC
                self.on_this_side += 1
            else:
                side, y_dis = self.kubik
                var = self.dir == 90 and (self.last_side is None or side != self.last_side)
                if self.last_dis is None or (y_dis > self.last_dis and not abs(y_dis - self.last_dis) < 2) or var:
                    self.kubik_ix = (self.kubik_ix + 1) % len(self.kubiks)
                    if self.seen_start and self.kubik_ix == len(self.kubiks) - 2:
                        self.lap_cnt += 1
                    elif not self.seen_start and self.kubik_ix == len(self.kubiks) - 1:
                        self.lap_cnt += 1
                    self.last_side = side
                    self.exec = KUBIK_TC
                    self.on_this_side += 1
                else:
                    self.idle_speed = 70
                    self.idle = True
                self.last_dis = y_dis
        else:
            for_dis = robot_car.find(max, scan, -2.5, 2.5)
            if for_dis is not None and for_dis <= 25:
                robot_car.shift_angle -= self.dir
                self.exec = FOR_WALL
                self.last_dis = None
                self.count += 1
            else:
                if for_dis is not None and for_dis <= 85 and self.narrow and self.wall_dis is not None:
                    self.narrow = False
                    if (self.dir == 90 and self.wall_dis < 55) or (self.dir == -90 and self.wall_dis < 60):
                        if self.dir == 90:
                            swing_dis = 60 - self.wall_dis
                        elif self.dir == -90:
                            swing_dis = self.wall_dis - 65
                        self.swing_ang = robot_car.dis_to_ang(swing_dis)
                        self.exec = NARROW
                    elif self.wall_dis > 70:
                        if self.dir == 90:
                            swing_dis = 70 - self.wall_dis
                        elif self.dir == -90:
                            swing_dis = self.wall_dis - 70
                        self.swing_ang = robot_car.dis_to_ang(swing_dis)
                        self.exec = NARROW
                else:
                    self.idle_speed = robot_car.calc_ccel(70, 80, for_dis, 120)
                    if for_dis is None or for_dis <= 70:
                        self.idle_speed = robot_car.calc_ccel(30, 45, for_dis, 120)
                    self.idle = True

    def reset_vars(self):
        self.kubik = None
        self.swing_ang = None
        self.idle_set = False
        self.skew_done = False
        self.manoeuvre = False
        self.color_val = False
        self.start_time = None
        self.gone_back = False
        self.last_ok = False
        self.get_close = False
        self.start_time = None
        self.face_kubik = False
        #self.start_pos = None
        self.last_back_dis = None
        self.back_dis = None

        self.exec = None

    def miav_callback(self):
        if robot_car.height_rot() < -10:
            robot_car.move(0,0)
            raise Exception
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

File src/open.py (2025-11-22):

#!/bin/python3

import math
import rclpy
import gpiozero
import robot_car
import rclpy.node
import sensor_msgs.msg

from rclpy.node import Node
from rclpy.qos import QoSProfile, QoSReliabilityPolicy

FOR_WALL = 0
FIX_GYRO_1 = 1
FIX_GYRO_2 = 2

CW_TRUST_SCORE = .3
CCW_TRUST_SCORE = .5

class miav(rclpy.node.Node):
    def __init__(self):
        super().__init__("miav")
        
        qos = QoSProfile(depth=10,reliability=QoSReliabilityPolicy.BEST_EFFORT)
        self.create_subscription(sensor_msgs.msg.LaserScan, '/scan', self.scan_callback, qos)
        self.create_timer(1.0 / 20.0, self.miav_callback)

        self.count = 0
        self.dir = None
        self.exec = None
        self.f_dir = False
        self.waitin = None
        self.pt_one = None
        self.pt_two = None
        self.idle_speed = 30
        self.start_pos = None

        robot_car.read_encoder()

    def scan_callback(self, msg):
        if self.exec is not None:
            return

        gyro_angle = robot_car.read_gyro()
        scan, rad = [], msg.angle_min
        for dis in msg.ranges:
            deg = math.degrees(rad) + 90
            if deg >= 180: deg -= 360
            deg = gyro_angle + deg
            dis *= 100
            if dis != 0 and math.isfinite(dis) and -130 <= deg <= 130 and dis >= 13:
                scan.append((deg, dis))
            rad += msg.angle_increment
        scan.sort()

        if not self.f_dir:
            for_dis = robot_car.find(min, scan, -3, 3)
            if for_dis is None or for_dis > 80:
                gyro_angle = robot_car.read_gyro()
                gyro_error = -gyro_angle
                robot_car.move(head = gyro_error * 2, speed = 60)
            else:
                left = robot_car.find(max, scan, -90, -10)
                right = robot_car.find(max, scan, 10, 90)
                if left is not None and (right is None or left > right):
                    self.dir = -90
                else:
                    self.dir = 90
                self.f_dir = True

        if not self.f_dir:
            return

        if self.dir == 90:
            self.side_dis = robot_car.find(min, scan, -100, -80)
        elif self.dir == -90:
            self.side_dis = robot_car.find(min, scan, 80, 100)

        if self.waitin is not None:
            self.exec, self.waitin = self.waitin, None
            return

        for_dis = robot_car.find(min, scan, -3, 3)
        var = for_dis is None or (self.count == 12 and for_dis > 180) or (self.count != 12 and \
                ((self.dir == 90 and for_dis > 60) or (self.dir == -90 and for_dis > 45)))
        if var:
            if for_dis is not None:
                if self.count != 12:
                    deaccel_speed = robot_car.calc_ccel(60, 80, for_dis, 170)
                else:
                    deaccel_speed = robot_car.calc_ccel(50, 60, for_dis, 100)
            else:
                deaccel_speed = 50
            self.idle_speed = deaccel_speed
        else:
            if self.count == 12:
                robot_car.move(0, 0)
                raise Exception
            else:
                robot_car.shift_angle -= self.dir
                self.exec = FOR_WALL
                self.count += 1

    def miav_callback(self):
        if robot_car.height_rot() > 10:
            robot_car.move(0, 0)
            raise Exception

        if self.exec is None:
            err = -robot_car.read_gyro()
            robot_car.move(err * 1.5, self.idle_speed)
        if self.exec is None: return
        if self.exec == FOR_WALL:
            gyro_angle = robot_car.read_gyro()
            gyro_error = -gyro_angle
            if not -5 <= gyro_error <= 5:
                gyro_angle = robot_car.read_gyro()
                gyro_error = -gyro_angle
                if self.dir == 90:
                    robot_car.move(head = gyro_error, speed = 30)
                else:
                    robot_car.move(head = gyro_error, speed = 30)
            else:
                self.exec = None
                self.waitin = FIX_GYRO_1
                robot_car.move(0, 0)
                print('turned')
        elif self.exec == FIX_GYRO_1:
            if self.pt_one is None:
                self.pt_one = self.side_dis
            if self.pt_one is not None:
                if self.start_pos is None and robot_car.pos is not None:
                    self.start_pos = robot_car.pos
                if robot_car.pos is None or robot_car.rot_to_cm(robot_car.pos - self.start_pos) < 20:
                    err = -robot_car.read_gyro()
                    robot_car.move(err * 2, 30)
                else:
                    self.exec = None
                    self.start_pos = None
                    robot_car.move(0, 0)
                    self.waitin = FIX_GYRO_2
                    print('fix_1')
        elif self.exec == FIX_GYRO_2:
            if self.pt_two is None:
                self.pt_two = self.side_dis
                slope = (self.pt_two - self.pt_one) / 20
                angle = math.degrees(math.atan(slope)) - robot_car.read_gyro()
                if self.dir == -90: angle = -angle + 4
                print('shift angle', angle)
                if self.dir == 90:
                    angle *= CW_TRUST_SCORE
                elif self.dir == -90:
                    angle *= CCW_TRUST_SCORE
                robot_car.shift_angle += angle
                robot_car.move(0, 0)
                self.pt_one = None
                self.pt_two = None
                self.exec = None
                print('fix_2')

b = gpiozero.Button(23)

def main():
    rclpy.init()
    node = miav()
    rclpy.spin(node)
    node.destroy_node()
    rclpy.shutdown()

if __name__ == '__main__':
    #b.wait_for_press()
    main()

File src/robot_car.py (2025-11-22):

import time
import math
import busio
import board
import serial
import gpiozero
import threading
import adafruit_bno055

ser = serial.Serial('/dev/ttyACM1', 115200)

ULTRA_ECHO = 25
ULTRA_TRIG = 24
GREEN_LED = 27
RED_LED = 22

i2c = busio.I2C(board.SCL, board.SDA)
gyro = adafruit_bno055.BNO055_I2C(i2c)

ultra = gpiozero.DistanceSensor(echo = ULTRA_ECHO, trigger = ULTRA_TRIG)
green_led = gpiozero.LED(GREEN_LED)
red_led = gpiozero.LED(RED_LED)

rot_to_cm_rate = 3.31 / 50
shift_angle = 0

max_pos = 138
min_pos = 42
pos = None

A = 11.8
B = -20

A_tc = 13.3
B_tc = -21

def dis_to_ang(dis, s = False):
    if s: return dis / abs(dis) * (A_tc * math.sqrt(abs(dis)) + B_tc)
    else: return dis / abs(dis) * (A * math.sqrt(abs(dis)) + B)

def calc_ccel(mn, mx, dis, cel):
    return max(min((mx - mn) * dis / cel + mn, mx), mn)

def rot_to_cm(rot):
    return abs(rot) * rot_to_cm_rate

def find(func, data, mn, mx):
    loc = None
    for deg, dis in data:
        if mn <= deg <= mx:
            if loc is None:
                loc = dis
            else:
                loc = func(loc, dis)
    return loc

def read_gyro():
    x = gyro.euler[0]
    if x > 180: x -= 360
    x += shift_angle
    while abs(x) > 360:
        if x > 0:   x -= 360
        else:       x += 360
    if x > 180:     x -= 360
    elif x < -179:  x += 360
    return x

def height_rot():
    return gyro.euler[2]

def norm(steer):
    return max(min(steer, max_pos), min_pos)

def move(head, speed):
    global cmd
    speed = int(speed)
    head = int(norm(90 + head))
    data = head.to_bytes(1, 'big') + speed.to_bytes(1, 'big', signed=True)
    checksum = (head + data[1]) & 0xFF
    frame = data + bytes([checksum])
    ser.write(frame)
    ser.flush()

def hard_brake():
    #move(0,0)
    move(0, 101)

def _encoder_loop():
    try:
        global pos
        buffer = bytearray()
        while True:
            buffer += ser.read(ser.in_waiting or 1)
            while len(buffer) >= 5:
                frame = buffer[:5]
                buffer = buffer[5:]
                data_bytes = frame[:4]
                checksum = frame[4]
                if sum(data_bytes) & 0xFF == checksum:
                    pos = int.from_bytes(data_bytes, 'big', signed=True)
                else:
                    buffer = buffer[1:]
            time.sleep(0.01)
    except Exception as e:
        print(e)

def read_encoder():
    thread = threading.Thread(target=_encoder_loop, daemon=True)
    thread.start()
